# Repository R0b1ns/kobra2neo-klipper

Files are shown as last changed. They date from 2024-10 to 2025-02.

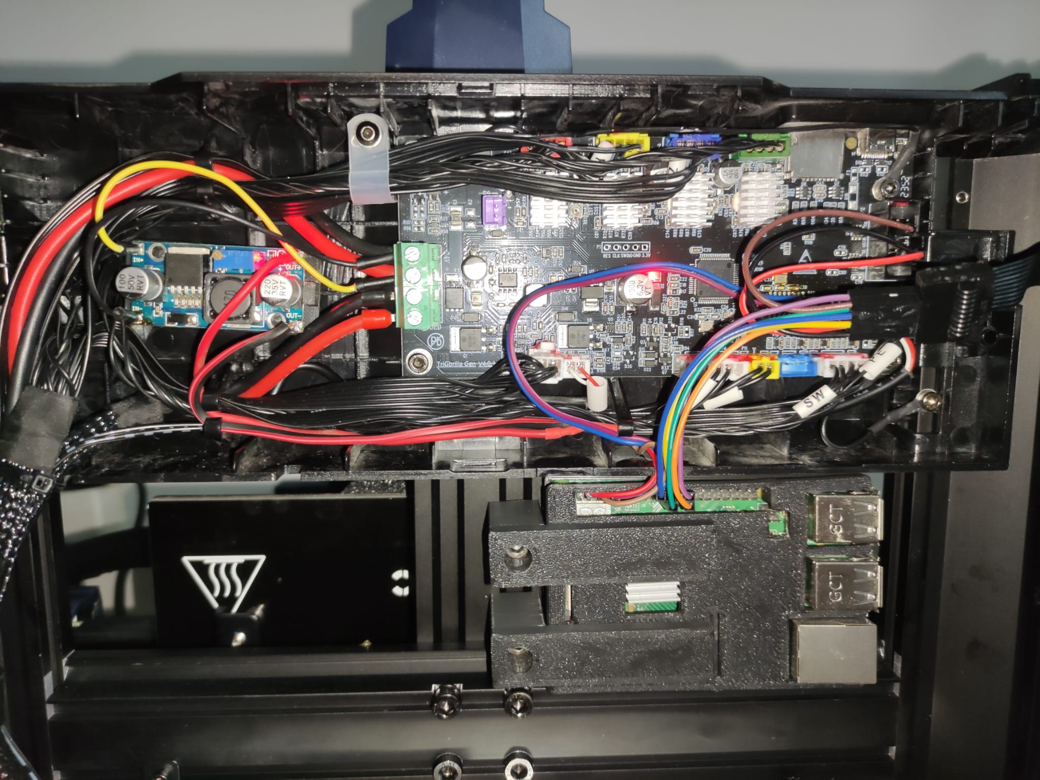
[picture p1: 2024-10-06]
ImagesMbWiring/Overview.jpg

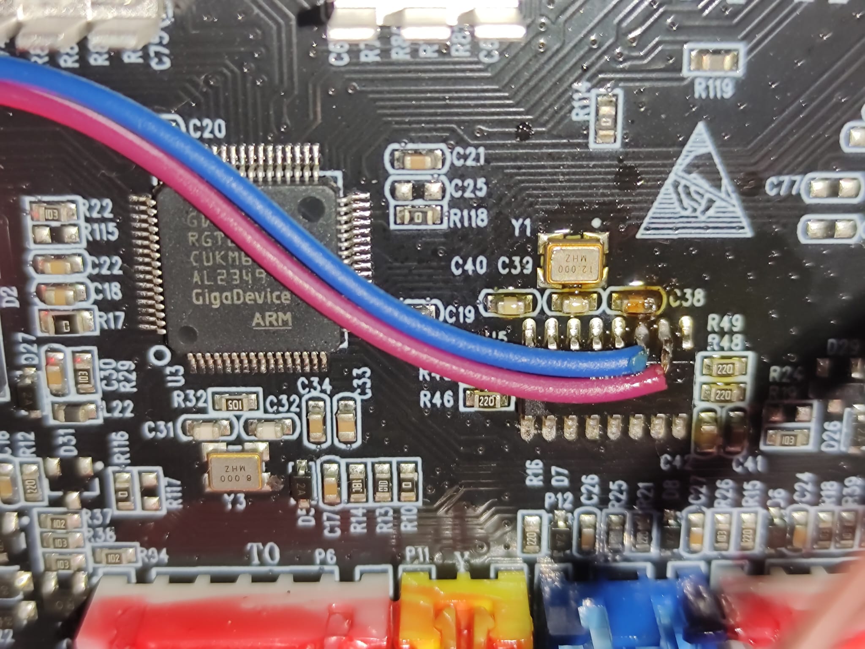
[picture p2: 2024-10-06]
ImagesMbWiring/USART-motherboard.jpg

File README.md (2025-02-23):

# Klipper on Anycubic Kobra 2 Neo

This repository provides a comprehensive guide and necessary resources for getting Klipper to work on the **Anycubic Kobra 2 Neo** 3D printer. It includes firmware, configuration files, profiles, wiring diagrams, and instructions for setting up Klipper and KlipperScreen on a Raspberry Pi.

## Directory Structure

- **CuraProfiles/**  
  Contains Cura profiles for the printer using the original stock firmware.
  
- **OriginalFirmware/**  
  Contains the stock firmware of the Anycubic Kobra 2 Neo, should you need to revert to the default setup.

- **ImagesMbWiring/**  
  Wiring diagrams and images that show how the Raspberry Pi is mounted and connected to the printer.

- **KlipperConfig/**  
  Configuration files for running Klipper on the Anycubic Kobra 2 Neo.

- **KlipperFirmware/**  
  Precompiled Klipper firmware files to be flashed onto the printer's controller board.

- **KlipperScreen/**  
  Instructions and files necessary for installing and setting up KlipperScreen on the Anycubic Kobra 2 Neo / Go screen connected to the Raspberry Pi.

- **OrcaSlicerProfiles/**  
  Slicing profiles for OrcaSlicer that are optimized for use with Klipper on the Anycubic Kobra 2 Neo.

- **RaspberryPiHolder/**  
  3D models for a custom holder mount to securely attach a Raspberry Pi to the printer.

## Getting Started

### 1. Preparing the Raspberry Pi

- Install the Raspberry Pi with a fresh copy of **Raspberry Pi OS**.
- Follow Klipper [documentation for installation via KIAHU](https://www.klipper3d.org/Installation.html#installing-via-kiauh).
- Follow the instructions in the `ImagesMbWiring/` directory to connect the Raspberry Pi to your Kobra 2 Neo printer (only if you want to use UART or KlipperScreen).

### 2. Flashing Klipper Firmware

- Download the appropriate firmware for your printer from the `KlipperFirmware/` directory.
- Flash the firmware to the printer's controller board as described unter `KlipperFirmware/README.md`.

### 3. Configuring Klipper

- Copy the contents of the `KlipperConfig/` directory to the Raspberry Pi, typically into the `~/printer_data/config` folder.
- Install moonraker dependencies. Connect via SSH, go to path `cd ~/` and clone dependencies:
```
git clone https://github.com/fluidd-core/fluidd-config.git
git clone https://github.com/protoloft/klipper_z_calibration.git
./klipper_z_calibration/install.sh
```
- Read comments of the `printer.cfg` and edit the configuration files as necessary based on your printer’s hardware. Default: USB mcu is configured
- Do not forget to do `PROBE_CALIBRATE` and bed mesh leveling.

### 4. Setting Up KlipperScreen (Optional)

- Follow the guide in the `KlipperScreen/` directory to set up KlipperScreen on a touchscreen connected to the Raspberry Pi. This provides an easy-to-use graphical interface for interacting with Klipper.

### 5. Slicer Profiles

- If you're using Cura, you can use the profiles in the `CuraProfiles/` directory for the stock firmware.
- For Klipper, it’s recommended to use OrcaSlicer with the profiles provided in the `OrcaSlicerProfiles/` directory for optimal performance.

### 6. Additional Resources

- Refer to the images in the `ImagesMbWiring/` folder for details on how to physically wire and mount the Raspberry Pi to your printer.
- If you need to revert back to the original firmware, you can find it in the `OriginalFirmware/` directory.

## Notes

- Adjust the configuration files according to your specific setup and hardware modifications.
- Ensure proper cooling and a proper PSU for your Raspberry Pi and other electronics to avoid overheating.
- I use a `LM2596` step-down module connected to the PSU to power the Raspberry Pi. Make sure you use proper gauge wires, otherwise you will experience power drop at load and throttle of the Raspberry Pi.
- Holder for `LM2596` is [here](https://www.thingiverse.com/thing:3324624/files).

## Contributions

Feel free to contribute to this repository by submitting pull requests or opening issues for any updates, corrections, or improvements.

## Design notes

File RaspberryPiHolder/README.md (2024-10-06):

# Kobra 2 Neo Raspberry Pi Mount

I've created a holder for the case. You can find the .STL here.

You need M4x20mm hex bolt and normal nut to mount.

Check the images in the [ImagesMbWiring](../ImagesMbWiring).

## Printed case

The case I use for [Raspberry Pi 3 is here](https://cults3d.com/en/3d-model/tool/raspberry-pi-3-slim-case-with-heatsink-cutout).

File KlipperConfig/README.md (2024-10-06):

# Kobra 2 Neo Klipper Config

These are the configuration files I'm using to run Klipper on Kobra 2 Neo.

---

## Warning

Before using this make sure you use `PROBE_CALIBRATE` and manually calibrate the z-offset.

Alternative you can check out the `Z_ENDSTOP_HIT` macro to get the offset. Read the comments first in the `macro.cfg`.

Then start to do you own bed mesh leveling!

In order to properly calibrate the z-offset and bed leveling you need set the temperature of the bed and extruder to the printing temperature you are using for the fillament you have. Make sure your noozle is wipe clean when you do this procedure.

---

## UART

You can also chose to use UART interface if you are fine with soldering two wires.

Check `printer.cfg` and the wiring images in the [ImagesMbWiring](../ImagesMbWiring).

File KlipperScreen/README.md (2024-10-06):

# Anycubic Kobra 2 Neo / GO LCD KlipperScreen

This will help you to set-up LCD for Anycubic Kobra 2 Neo, Kobra Go equipped with Klipper and Raspberry Pi.
Make sure you already have [KlipperScreen installed](https://klipperscreen.readthedocs.io/en/latest/Installation/).

## Power Connections
You can use power from the in-built printer PCB or the Raspberry Pi (RPI).

- **5V** -> 5V
- **GND** -> GND

## SPI Connections
- **SCK** -> GPIO 11 (SPI SCLK)
- **MOSI** -> GPIO 10 (SPI MOSI)
- **CS** -> GPIO 8 (SPI CE0)
- **RESET** -> GPIO 25
- **DC** (marked as MISO on the mainboard) -> GPIO 24

You can find images in the [ImagesMbWiring](../ImagesMbWiring).

For images and more details, check the [Hardware Setup](https://github.com/jokubasver/Anycubic-Kobra-Go-Neo-LCD-Driver?tab=readme-ov-file#hardware-setup).

---

## Installation

You can install the LCD firmware binary by simply copy it to `/lib/firmware/`:

1. Clone the repository:

    ```bash
    git clone https://github.com/cheadrian/kobra2neo-klipper
    ```

2. Navigate to the firmware directory:

    ```bash
    cd ~/kobra2neo-klipper/KlipperScreen
    ```
3. Copy the firmware binary to the system:

    ```bash
    sudo cp kobra2neo-lcd.bin /lib/firmware/
    ```
   Now you go bellow to see how to modify `config.txt`.
---

## Creating the LCD Firmware Binaries

Optional: if you want to modify the LCD init command.

To create the firmware binary from scratch follow these steps:

1. Set the appropriate permissions for the command tool:

    ```bash
    chmod 755 mipi-dbi-cmd
    chmod +x mipi-dbi-cmd
    ```

2. Create the firmware binary:

    ```bash
    ./mipi-dbi-cmd kobra2neo-lcd.bin kobra2neo-lcd.txt
    ```

3. Copy the firmware binary to the system:

    ```bash
    sudo cp kobra2neo-lcd.bin /lib/firmware/
    ```

For tool information, check [this link](https://github.com/notro/panel-mipi-dbi/wiki).

---

## Raspberry Pi configuration

**Note:** If you're using a UART interface for Klipper-MCU communication, follow the steps below. If you're using a USB connection for Klipper, you can skip these lines.

1. Open the configuration file:

    ```bash
    sudo nano /boot/firmware/config.txt
    ```
	
2. Disable vc4-kms by commenting this line:

	```bash
	# dtoverlay=vc4-kms-v3d
	```

3. Add the following lines to enable UART and set up the LCD overlay:

    ```bash
    [all]
    # Enable UART interface for Klipper-MCU communication
    enable_uart=1
    dtoverlay=disable-bt
    
    # Set up LCD overlay and firmware details
    dtoverlay=mipi-dbi-spi,spi0-0,speed=32000000
    dtparam=compatible=kobra2neo-lcd\0panel-mipi-dbi-spi
    dtparam=write-only,cpha,cpol
    dtparam=width=320,height=240,width-mm=49,height-mm=37
    dtparam=reset-gpio=25,dc-gpio=24
	
	# Disable RPI splashscreen
	disable_splash=1
	
    ```
	
4. Display the kernel boot console at start up:

	```bash
	sudo nano /boot/firmware/cmdline.txt
	```
	
	Append this at the end:

	```bash
	fbcon=map:1 logo.nologo quiet
	```

5. Save and reboot:

    ```bash
    sudo reboot
    ```

---

## Control the interface

While the Kobra 2 Neo / Go doesn't have touchscreen, you can control interface by using an USB mouse or configure the rotary encoder to act as one.

You can find more details [about encoder here](https://github.com/SomeSpaceNerd/KlipperScreen-Encoder-Driver).

To display the cursor on KlipperScreen simply create `KlipperScreen.conf` in MainSail / Fluidd config and enter:

```bash
[main]
show_cursor: True
```

---

## Relevant Documentation

- [ILI9341V Display Controller Datasheet](https://www.orientdisplay.com/pdf/ILI9341V.pdf)
- [ST7796s Display Controller Datasheet](https://www.displayfuture.com/Display/datasheet/controller/ST7796s.pdf)

---

### `kobra2neo-lcd.txt` is based on [this discussion](https://forums.raspberrypi.com/viewtopic.php?p=2207118#p2207118).

---

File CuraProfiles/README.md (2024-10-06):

# Kobra 2 Neo CURA profile

This is a backup of the CURA configuration for Kobra 2 Neo with **stock firmware**.

It is not compatible with Klipper. Use OrcaSlicer for Klipper.

---

## Installation
Replace the files in the:

`C:\Users\<YOUR_PC_USERNAME>\AppData\Roaming\cura\5.8`

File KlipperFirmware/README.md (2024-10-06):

# Kobra 2 Neo Klipper Firmware

There are two versions of Klipper firmware:

	- klipper_usart.bin - if you want connect to printer PCB using UART interface of the Raspberry Pi, baud rate 115200
	- klipper_usb.bin - if you want to use the USB connection between Raspberry Pi and the printer, baud rate 250000

---

## Installation
Put the firmware to the micro SDCard and rename it to `firmware.bin`, power up the printer, wait 1 minute, power off the printer and pull out the micro SDCard, enjoy.

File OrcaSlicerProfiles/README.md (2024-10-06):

# Kobra 2 Neo OrcaSlicer profile

This is a backup of the OrcaSlicer configuration for Kobra 2 Neo with **Klipper firmware**.

It is not compatible with stock firmware. Use Cura for stock firmware.

---

## Installation
Replace / add the files in the:

`C:\Users\<YOUR_PC_USERNAME>\AppData\Roaming\OrcaSlicer\user`

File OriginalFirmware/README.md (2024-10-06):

# Kobra 2 Neo Klipper Firmware

If you want to revert to the stock firmware for Kobra 2 Neo.

---

## Installation
Put the firmware to the micro SDCard and rename it to `firmware.bin`, power up the printer, wait 1 minute, power off the printer and pull out the micro SDCard, enjoy.

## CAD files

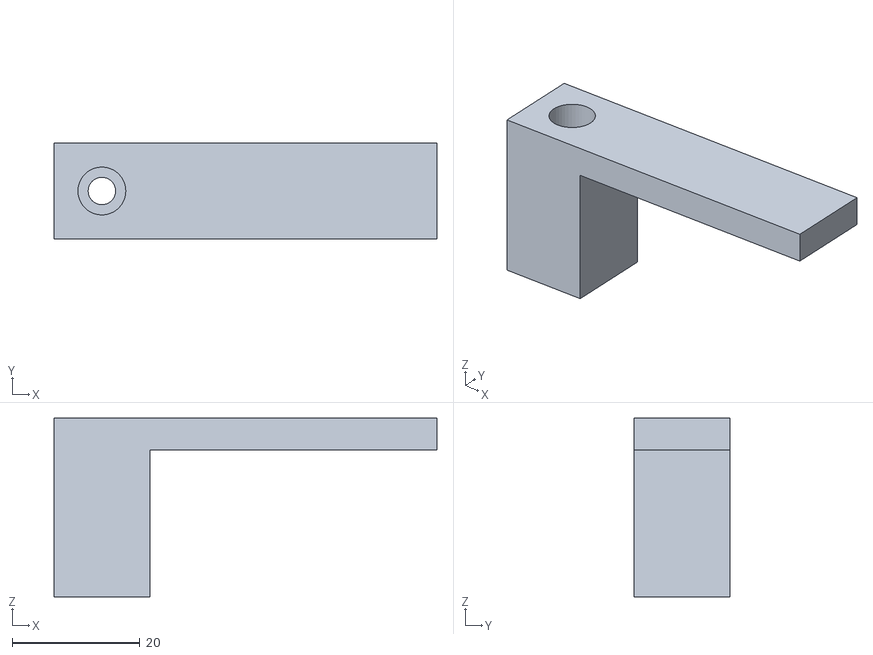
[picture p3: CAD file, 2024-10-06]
RaspberryPiHolder/Raspberry_Case_Holder.stl
60.0 x 15.0 x 28.0

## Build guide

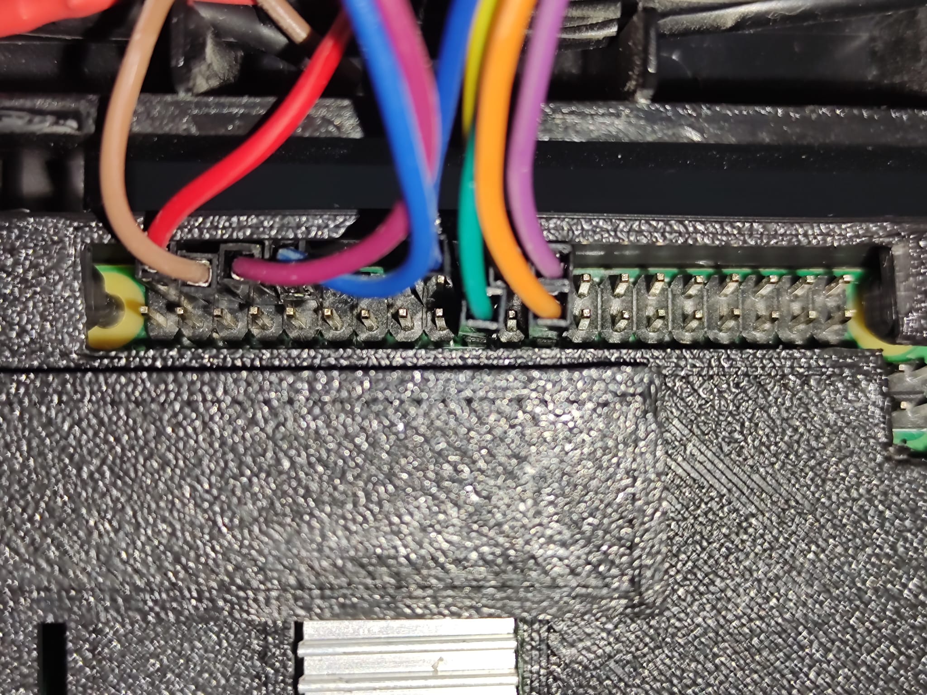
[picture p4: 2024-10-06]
ImagesMbWiring/RaspberryPi-Screen.jpg

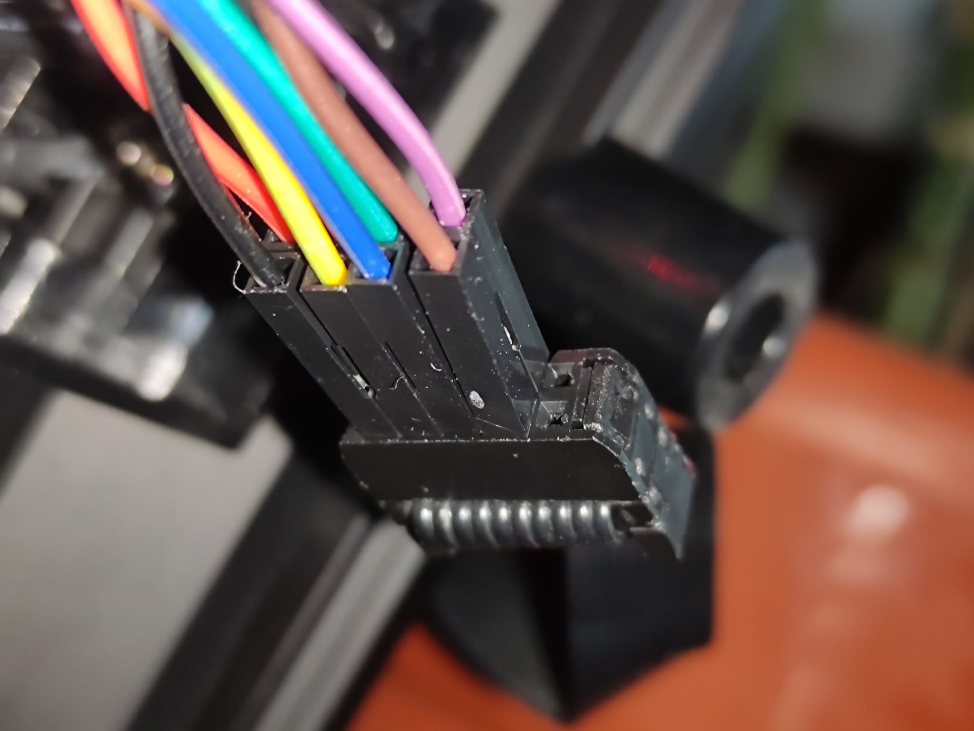
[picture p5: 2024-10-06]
ImagesMbWiring/ScreenConnector (2).jpg

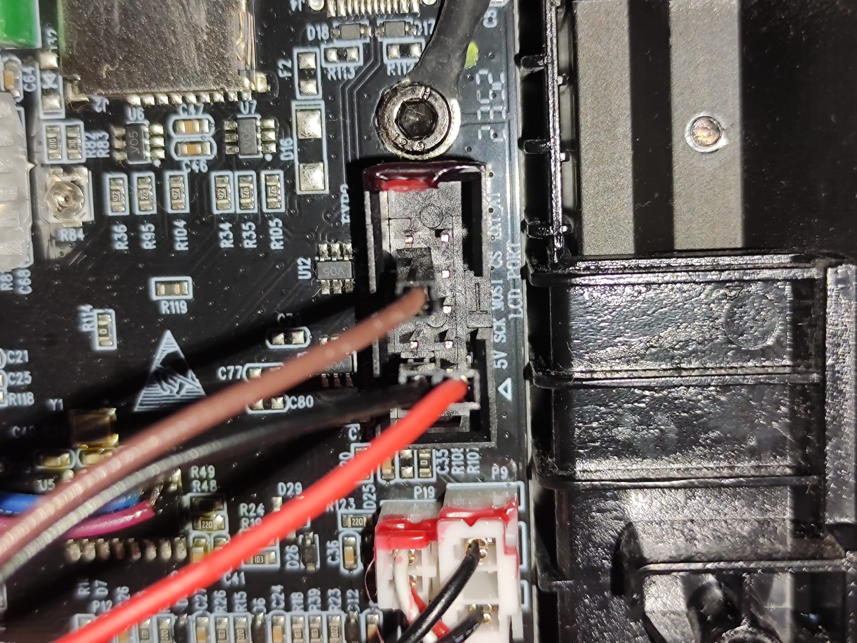
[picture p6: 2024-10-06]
ImagesMbWiring/ScreenConnector.jpg

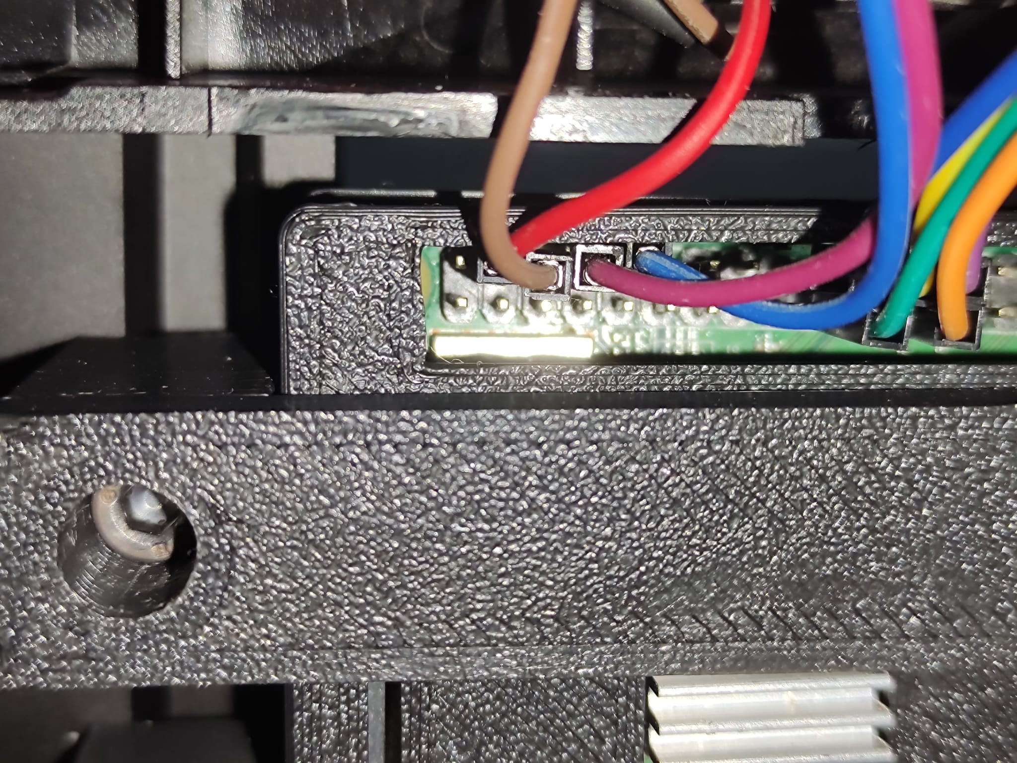
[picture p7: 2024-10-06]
ImagesMbWiring/RaspberryPi-USART.jpg

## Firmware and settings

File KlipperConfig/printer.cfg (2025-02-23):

#################################################
# Based on j0tp3, zamonary1 configs.
# Adapted to work with USART, auto z-home endstop, 
# rotary encoder cancel print.
#################################################


[include fluidd.cfg]
[include macros.cfg]
# AutoZ configuration is not done
# [include autoz.cfg]


[exclude_object]
[gcode_arcs]

[mcu]
restart_method: command
# If you are using USB:
serial: /dev/serial/by-id/usb-1a86_USB_Serial-if00-port0
baud: 250000
# If you are using UART (make sure to edit the Raspberry Pi config.txt):
# serial: /dev/ttyAMA0
# baud: 115200

[printer]
kinematics: cartesian
max_velocity: 300
max_accel: 10000
max_z_velocity: 8
max_z_accel: 800

[virtual_sdcard]
path: ~/printer_data/gcodes
on_error_gcode: CANCEL_PRINT

[input_shaper]
shaper_freq_x: 54.8
shaper_type_x: ei
shaper_freq_y: 34.0
shaper_type_y: mzv

[stepper_x]
step_pin: PA12
dir_pin: PA11
enable_pin: !PA15
microsteps: 16
rotation_distance: 40
endstop_pin: ^!PB11
position_endstop: -5.8
position_min: -5.8
position_max: 230
homing_speed: 100

[stepper_y]
step_pin: PA9
dir_pin: !PA8
enable_pin: !PA15
microsteps: 16
rotation_distance: 40
endstop_pin: ^!PC13
position_endstop: -1.0
position_min: -1.0
position_max: 240
homing_speed: 100

[stepper_z]
step_pin: PB0
dir_pin: !PB1
enable_pin: !PA15
microsteps: 16
rotation_distance: 8
# (1/3) Enable this for PA0 Probe button
# PA0 is 3mm below Bed?
# position_endstop: -3
# Define endstop PIN (z calibration button)
# endstop_pin: PA0
# Normal homing behaviour
endstop_pin: probe:z_virtual_endstop
position_min: -4
position_max: 250
homing_speed: 15
second_homing_speed: 1

[extruder]
max_extrude_cross_section: 5.0 
step_pin: PB15
dir_pin: PB14
enable_pin: !PA15
microsteps: 16
max_extrude_only_distance: 200
max_extrude_only_velocity: 80
max_extrude_only_accel: 5000
rotation_distance: 7.084
nozzle_diameter: 0.400
filament_diameter: 1.750
# Tune this with the documentation https://www.klipper3d.org/Pressure_Advance.html
# Or with https://www.obico.io/blog/pressure-advance-calibration-in-orca-slicer-a-comprehensive-guide/
pressure_advance: 0.0400
heater_pin: PB8
sensor_type: ATC Semitec 104GT-2
sensor_pin: PC3
min_extrude_temp: 175
min_temp: 0
max_temp: 250
# Tune this with this guide https://www.obico.io/blog/klipper-pid-tuning/
control: pid
pid_ki: 0.88
pid_kd: 59.12
pid_kp: 14.42 
#pressure advance

[heater_bed]
heater_pin: PB9
sensor_type: EPCOS 100K B57560G104F
sensor_pin: PC1
min_temp: 0
max_temp: 120
# Tune this with this guide https://www.obico.io/blog/klipper-pid-tuning/
control: pid
pid_kp: 97.1 
pid_ki: 1.41
pid_kd: 1675.16

[probe]
pin: PA1
x_offset : 24.0
y_offset : 13.35
# This parameter must be provided.
z_offset: 1.7
samples: 3
samples_result: average
samples_tolerance_retries: 1
sample_retract_dist: 2
speed: 15
lift_speed: 8
samples_tolerance : 0.1
samples_tolerance_retries : 3

[bed_mesh]
speed: 200
horizontal_move_z: 5
# TODO: Improve that
# min: 0 + relative to probe + 2 (24 + 2),(14 + 2)
mesh_min: 26, 16
# max: 230 - relative to probe - 2: (230 - 24 - 2), (230 - 13 - 2)
mesh_max: 204, 215
probe_count: 5,5
mesh_pps: 4,4 
algorithm: bicubic
bicubic_tension: 0.2

# Z-home probing, position for z-button
# WARNING! Only enable this if other config for Probe button is done!
# !!! Otherwise the nozzle will not stop and smash your button / bed !!!
# (2/3) Enable this for PA0 Probe button
# [safe_z_home]
## Coordinates must be changed to center of your button
# home_xy_position: 64.10, 238.80
# speed: 100
# z_hop: 5
# z_hop_speed: 15

[safe_z_home]
# z-home probing with magnetic probe.
# Coordinates of left end of the bed, like anycubic firmware does it
# WARNING! Sensor position has to be over the bed. 
home_xy_position: 40, 190
speed: 100
z_hop: 5
z_hop_speed: 15

#[firmware_retraction]
#retract_length: 1.8
#retract_speed: 50
##unretract_extra_length: 0
#unretract_speed: 50

[controller_fan controller_fan]
pin: PB12

[heater_fan extruder_fan]
pin: PB13

[fan]
pin: PB5
cycle_time: 0.00005 #20kHz

# This pin enables the bed, hotend, extruder fan, part fan.
[output_pin enable_pin]
pin: PB6
value: 1

# If you want to use the rotary button press to cancel the running print
[gcode_button pb4]
pin: PB4
press_gcode: CANCEL_PRINT
#release_gcode:

# (3/3) Disable this for PA0 Probe button
# This is for the Anycubic Kobra printers equipped with auto Z-home button
[gcode_button z_calibration_button]
pin: PA0
press_gcode: 
    QUERY_BUTTON button=z_calibration_button

    # RESPOND TYPE=command MSG='Z-endstop touched!'
    # M114
release_gcode:
    QUERY_BUTTON button=z_calibration_button
 
[respond]
default_type: echo
default_prefix:

[temperature_sensor raspberry_pi]
sensor_type: temperature_host
min_temp: 10
max_temp: 100

[temperature_sensor mcu_temp]
sensor_type: temperature_mcu
min_temp: 0
max_temp: 100

[save_variables]
filename: ~/printer_data/config/variables.cfg

#*# <---------------------- SAVE_CONFIG ---------------------->
#*# DO NOT EDIT THIS BLOCK OR BELOW. The contents are auto-generated.
#*#
#*# [probe]
#*#
#*# [bed_mesh default]
#*# version = 1
#*# points =
#*#       -0.110000, -0.125833, -0.133333, -0.120833, -0.062500, 0.035833, 0.164167
#*#       -0.075833, -0.088333, -0.091667, -0.074167, -0.010833, 0.081667, 0.215000
#*#       0.003333, -0.015000, -0.029167, -0.022500, 0.040000, 0.121667, 0.246667
#*#       -0.046667, -0.065833, -0.076667, -0.077500, -0.013333, 0.066667, 0.191667
#*#       -0.033333, -0.061667, -0.103333, -0.111667, -0.055000, 0.019167, 0.134167
#*#       -0.215000, -0.255833, -0.285833, -0.283333, -0.221667, -0.142500, -0.020000
#*#       -0.270000, -0.325000, -0.340833, -0.317500, -0.255833, -0.163333, -0.039167
#*# x_count = 7
#*# y_count = 7
#*# mesh_x_pps = 4
#*# mesh_y_pps = 4
#*# algo = bicubic
#*# tension = 0.2
#*# min_x = 26.0
#*# max_x = 203.96
#*# min_y = 16.0
#*# max_y = 214.95999999999998

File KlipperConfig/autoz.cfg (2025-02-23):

##### WARNING! ZButton PA0 is not configured here. Skript under DEV. Could harm your device!

[z_calibration]

# default from home_xy_position of safe_z_home
nozzle_xy_position: 40, 190
#   A X, Y coordinate (e.g. 100,100) of the nozzle, clicking on the z endstop.
switch_xy_position: 64.10, 238.80
#   A X, Y coordinate (e.g. 100,100) of the probe's switch body, clicking on
#   the z endstop.
switch_xy_offsets: -24.10, -48.80
#   Instead of an absolute position (switch_xy_position), this configuration
#   adds an X, Y offset (e.g. -6,-18) to the nozzle position.
bed_xy_position: 115, 115
#   A X, Y coordinate (e.g. 100,100) where the print surface (e.g. the center
#   point) is probed. These coordinates are adjusted by the
#   probe's X and Y offsets. The default is the zero_reference_position which
#   replaces the deprecated relative_reference_index
#   of the configured bed_mesh, if configured. It's possible to change the zero
#   reference position at runtime or use the GCode argument BED_POSITION of CALIBRATE_Z.
wiggle_xy_offsets: 0,0
#   After probing the nozzle and retracting, move x some distance away and
#   back. Useful to prevent the z endstop pin sticking to the nozzle and
#   being pulled out of the assembly. Can be negative. Defaults to zero to
#   disable it. Can be combined in x and y to move diagonally. Be careful
#   to not move your nozzle out of range!
switch_offset: 0.10
#   The trigger point offset of the used mag-probe switch.
#   A larger value will position the nozzle closer to the bed.
#   This must be determined manually. More on this later
#   in this section..
offset_margins: -1.0,1.0
#   The minimum and maximum margins allowed for the calculated offset.
#   If the offset is outside these values, it will stop!
#   The margin can be defined as "min,max" e.g. "-0.5,1.5" or by just one
#   value e.g. "1.0" which translates to "-1.0,1.0" (which is also the default).
# max_deviation: DEPRECATED - please use offset_margins instead!
#   The maximum allowed deviation of the calculated offset.
#   If the offset exceeds this value, it will stop!
#   The default is 1.0 mm.
# samples: default from "probe:samples" section
#   The number of times to probe each point. The probed z-values
#   will be averaged. The default is from the probe's configuration.
# samples_tolerance: default from "probe:samples_tolerance" section
#   The maximum Z distance (in mm) that a sample may differ from other
#   samples. The default is from the probe's configuration.
# samples_tolerance_retries: default from "probe:samples_tolerance_retries" section
#   The number of times to retry if a sample is found that exceeds
#   samples_tolerance. The default is from the probe's configuration.
# samples_result: default from "probe:samples_result" section
#   The calculation method when sampling more than once - either
#   "median" or "average". The default is from the probe's configuration.
# safe_z_height: default is 2 * z_offset from the "probe:z_offset" section
#   The absolute z position in mm to move to before moving to the next
#   position. The default is two times the z_offset from the probe's
#   configuration. The minimum safe z height is 3mm.
# clearance: DEPRECATED - please use safe_z_height instead!
#   The distance in mm to move up before moving to the next
#   position. The default is two times the z_offset from the probe's
#   configuration.
# position_min: default from "stepper_z:position_min" section.
#   Minimum valid distance (in mm) used for probing move. The
#   default is from the Z rail configuration.
speed: 50
#   The moving speed in X and Y. The default is 50 mm/s.
# lift_speed: default from "probe:lift_speed" section
#   Speed (in mm/s) of the Z axis when lifting the probe between
#   samples and clearance moves. The default is from the probe's
#   configuration.
# probing_speed: default from "stepper_z:homing_speed" section.
#   The fast probing speed (in mm/s) used, when probing_first_fast
#   is enabled. The default is from the Z rail configuration.
# probing_second_speed: default from "stepper_z:second_homing_speed" section.
#   The slower speed (in mm/s) for probing the recorded samples.
#   The default is second_homing_speed of the Z rail configuration.
# probing_retract_dist: default from "stepper_z:homing_retract_dist" section.
#   Distance to retract (in mm) before probing the next sample.
#   The default is homing_retract_dist from the Z rail configuration.
#   Caution: if sensorless homing is used on the Z axis with
#   homing_retract_dist set to zero, this must be set to a value greater zero.
probing_first_fast: false
#   If true, the first probing will be faster by the probing speed.
#   This is to get down faster and not record the result as a
#   probing sample. The default is false.
start_gcode: M401
#   A list of G-Code commands to run before each calibration command.
#   See docs/Command_Templates.md for the G-Code format. This can be used to
#   attach the probe.
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

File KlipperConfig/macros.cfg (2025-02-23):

[gcode_macro Z_ENDSTOP_HIT]
gcode:
  {% set Z_ENDSTOP_HIT = printer.save_variables.variables.z_endstop_hit | default(0) | float | round(3) %}
  RESPOND TYPE=command MSG="Reset z_endstop_hit from {Z_ENDSTOP_HIT} to 0.0"
  SAVE_VARIABLE VARIABLE=z_endstop_hit VALUE=0
  G90
  # Note: you need to adjust the position to the center of the button!
  G1 X64.10 Y238.80 Z5 F8000
  # TODO -> Add retraction and wipe, make sure it is in center!
  M400
  # Note: you need to adjust the position to the center of the button!
  G1 X64.10 Y238.80 Z3 F500
  M400
  G91
  {% set z_count = 500 %}
  {% for cz in range(z_count) %}
    _MOVE_Z_DOWN
  {% endfor %}

[gcode_macro _MOVE_Z_DOWN]
gcode:
  {% if printer.save_variables.variables.z_endstop_hit == 0 %}
    G1 Z-0.01 F50
    M400
    _CHECK_Z_HIT
  {% endif %} 
  
[gcode_macro _CHECK_Z_HIT]
variable_z_end: 0
gcode:
    {% set Z_POSITION = printer.toolhead.position.z | default(0) | float | round(3) %}
    {% set Z_PROBE_OFFSET = printer.configfile.settings.probe.z_offset | default(0) | float | round(3) %}
    {% set Z_PRINTBED_OFFSET = printer.save_variables.variables.z_printbed_offset | default(0.4) | float | round(3) %}

    {% if printer['gcode_button z_calibration_button'].state == "PRESSED" %}
        RESPOND TYPE=command MSG="Z-end button hit at {Z_POSITION}"
        SAVE_VARIABLE VARIABLE=z_endstop_hit VALUE={Z_POSITION}
        {% set CALCULATED_Z_PROBE_OFFSET = Z_PROBE_OFFSET + Z_POSITION * -1 - Z_PRINTBED_OFFSET %}
        SAVE_VARIABLE VARIABLE=z_calculate_probe VALUE={CALCULATED_Z_PROBE_OFFSET}
        RESPOND TYPE=command MSG="Manually modify the probe z-offset in the printer.cfg to {CALCULATED_Z_PROBE_OFFSET}"
    {% endif %}

[gcode_macro PULL_FILAMENT_OUT]
gcode:
  G91
  G1 E20 F500
  G1 E-100 F500
  G90
  M84 #motors off

[gcode_macro FILAMENT_INSERT]
gcode:
  G91
  G1 E40 F500 #extrude 40mm of filament
  G90
  M84 #motors off

[gcode_macro PRINT_END]
 gcode:
  M106 S0
  G91
  G1 E-2
  G1 Z5 F200
  G90
  
  G1 F2000 X20
  G1 F2500 Y200 ; expose the print
  M140 S0
  M104 S0
  M84 #motors off

[gcode_macro CANCEL_PRINT]
gcode:
  TURN_OFF_HEATERS
  CANCEL_PRINT_BASE
  G91
  G0 Z10 F3600 ; move nozzle up
  G90
  G0 X125 Y200 F20000 ; move nozzle to remove stringing
  M107 ; turn off fan
  G90 ; absolute positioning
  BED_MESH_CLEAR

[gcode_macro DRY_FILAMENT]
gcode:
  SET_HEATER_TEMPERATURE HEATER=heater_bed TARGET=60
  G4 P10800000 #3 hours (3*60*60*1000)
  SET_HEATER_TEMPERATURE HEATER=heater_bed TARGET=0

[gcode_macro START_PRINT]
gcode:
  {% set BED_TEMP = params.BED_TEMP|default(60)|float %}
  {% set EXTRUDER_TEMP = params.EXTRUDER_TEMP|default(190)|float %}

  # Start bed heating
  M140 S{BED_TEMP}

  # Start hotend heating
  M104 S{EXTRUDER_TEMP}

  # Wait for bed to reach temperature
  M190 S{BED_TEMP}
  
  # Set and wait for nozzle to reach temperature
  M109 S{EXTRUDER_TEMP}

  # Load default bed mesh
  BED_MESH_PROFILE LOAD="default"

  # Set absolute position
  G90
  
  # Home the printer
  G28 X Y Z

  # Move head to the other side
  G1 X50 Y0 Z3 F1200

  # Draw a line
  G92 E0  ;zero the extruded length
  G1 X70 Y-2 Z0.6 F2400                ; that's scary
  G1 E3 F1000
  G1 X130  E43 F500                       ; Extrude 45mm of filament in a 6cm line.
  G1 Z1

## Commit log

2024-10-06 Kobra 2 Klipper
    [macros.cfg, printer.cfg, variables.cfg]
2024-10-06 Add STL for Raspberry Pi holder
    [Raspberry_Case_Holder.stl]
2025-02-23 Fix USB MCU, Corrected stepper boundaries; Added comments and warnings
    Fix mcu config USB Serial device was set, but UART baud; Fixed wrong stepper boundaries. X_min=-14 made knocking sounds!; probe: Added missing and required z_offset; Updated bed_mesh cause boundaries were changed, here is room for improovements; safe_z_home: Set position to left end of the bed, like anycubic firmware does it; Added info and warnings for PA0 probe button config, since this config smashed by probe button / bed; renamed gcode_button to z_calibration_button
    [autoz.cfg, macros.cfg, printer.cfg]
